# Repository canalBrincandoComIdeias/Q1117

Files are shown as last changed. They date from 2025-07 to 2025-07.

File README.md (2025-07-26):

# Q1117
**Painéis I2C para o Elevador**

Projeto do Vídeo Q1117 Série **_Tutorial Maker_** powered by **_Petrobras_**

:video_camera: Assista o vídeo [CLIQUE AQUI](https://youtu.be/gxso-JEM9QQ)

- Confira a série completa na Playlist [(Clique Aqui)](https://www.youtube.com/playlist?list=PL7CjOZ3q8fMfSiij6-3jm6nDhk7XdAp0p)

:mortar_board: Aprenda a programar ARDUINO com nossos cursos e aprenda a desenvolver sua própria lógica da programação e ter uma maior independencia, sem precisar copiar sketchs na internet.
- [Curso de Arduino para Principiantes](https://cursodearduino.net/principiantes/) 
- [Curso de Arduino 2.0](https://cursodearduino.net/)

:iphone: Todos os apps Android **Brincando com Ideias**: [CLIQUE AQUI](https://play.google.com/store/apps/developer?id=Brincando+com+Ideias&hl=pt_BR) 

 - Aplicativo montTUDO 4 canais: [CLIQUE AQUI](https://play.google.com/store/apps/details?id=appinventor.ai_thiago_vilella.montTUDO_4_Canais)
 - Aplicativo monTUDO robô: [CLIQUE AQUI](https://play.google.com/store/apps/details?id=appinventor.ai_flaviosg_2407.montTUDO_Robo)

**Conheça nossas Redes Sociais:**









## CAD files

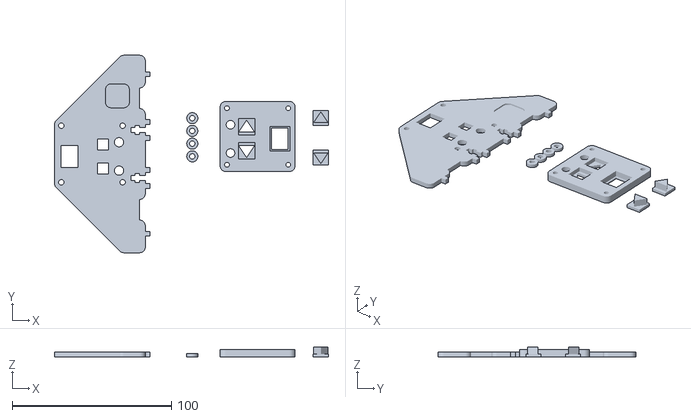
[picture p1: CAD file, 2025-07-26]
KK.128 - Painel de Andar do Elevador - Impressao.stl
172.0 x 124.0 x 6.00

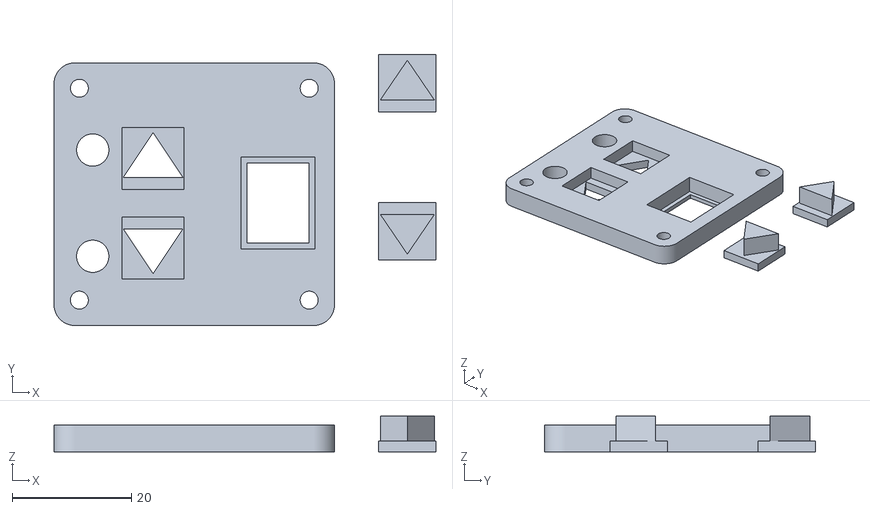
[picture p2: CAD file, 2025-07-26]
K.128 - Painel de Andar do Elevador - Impressao 3D.stl
64.0 x 45.4 x 6.00

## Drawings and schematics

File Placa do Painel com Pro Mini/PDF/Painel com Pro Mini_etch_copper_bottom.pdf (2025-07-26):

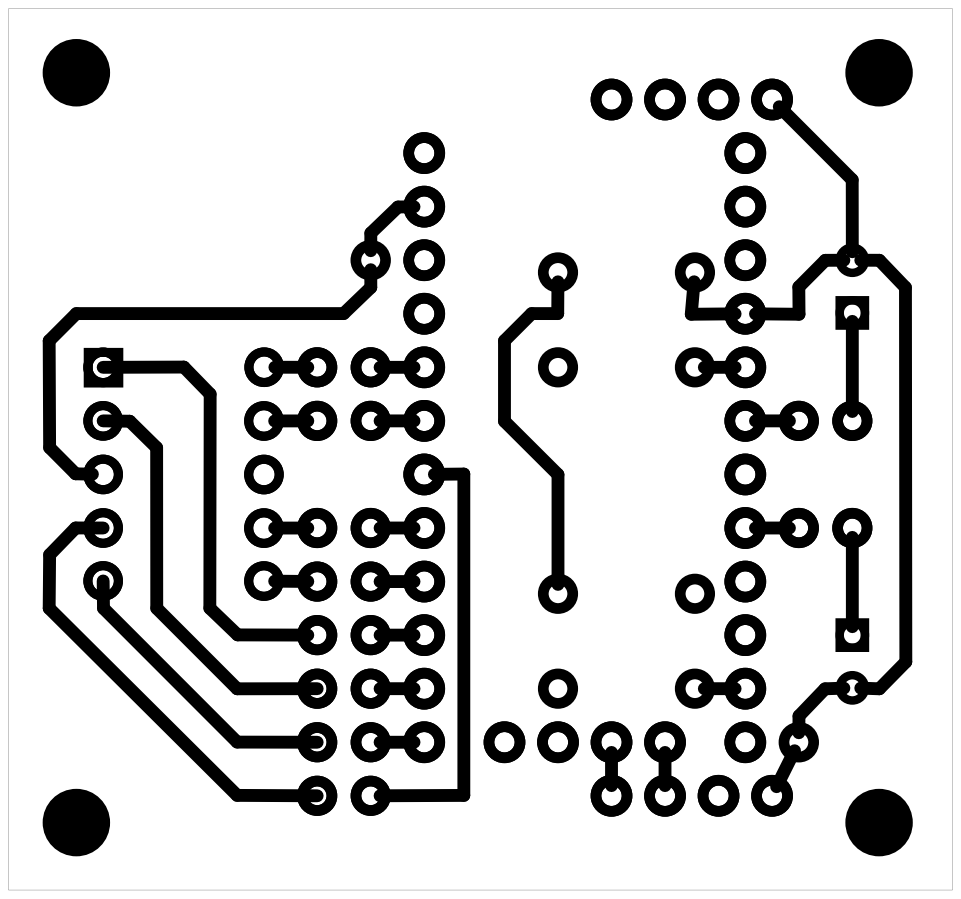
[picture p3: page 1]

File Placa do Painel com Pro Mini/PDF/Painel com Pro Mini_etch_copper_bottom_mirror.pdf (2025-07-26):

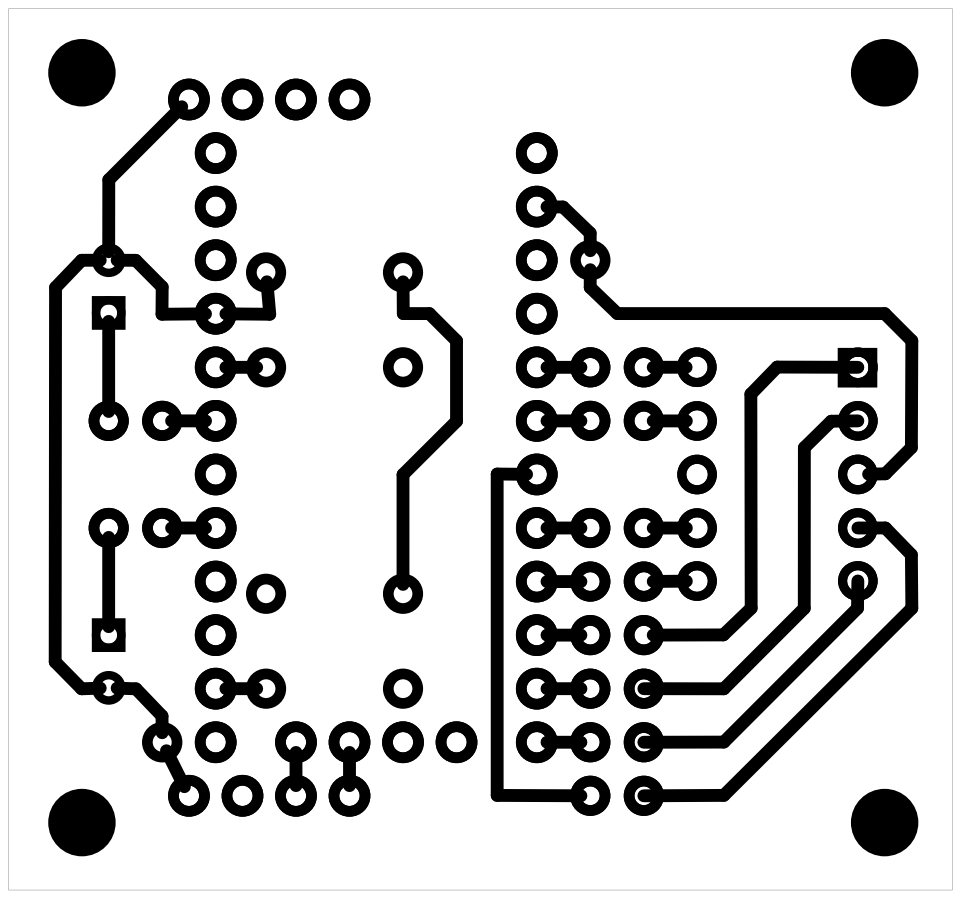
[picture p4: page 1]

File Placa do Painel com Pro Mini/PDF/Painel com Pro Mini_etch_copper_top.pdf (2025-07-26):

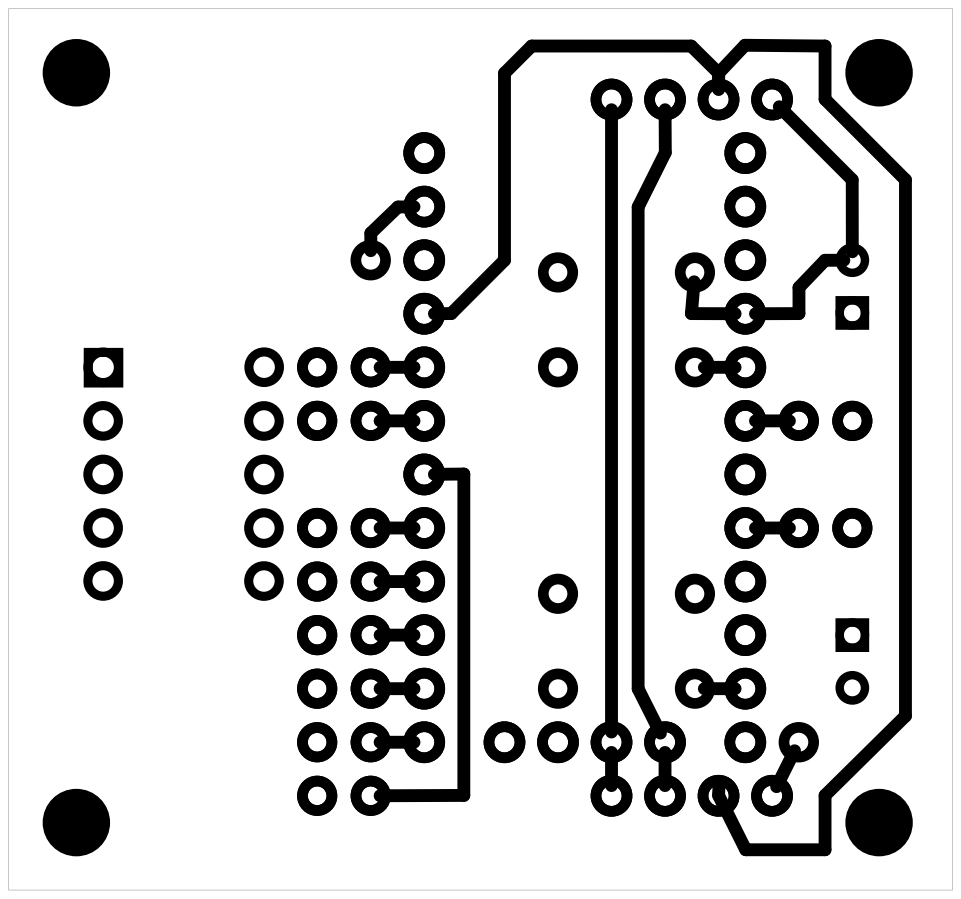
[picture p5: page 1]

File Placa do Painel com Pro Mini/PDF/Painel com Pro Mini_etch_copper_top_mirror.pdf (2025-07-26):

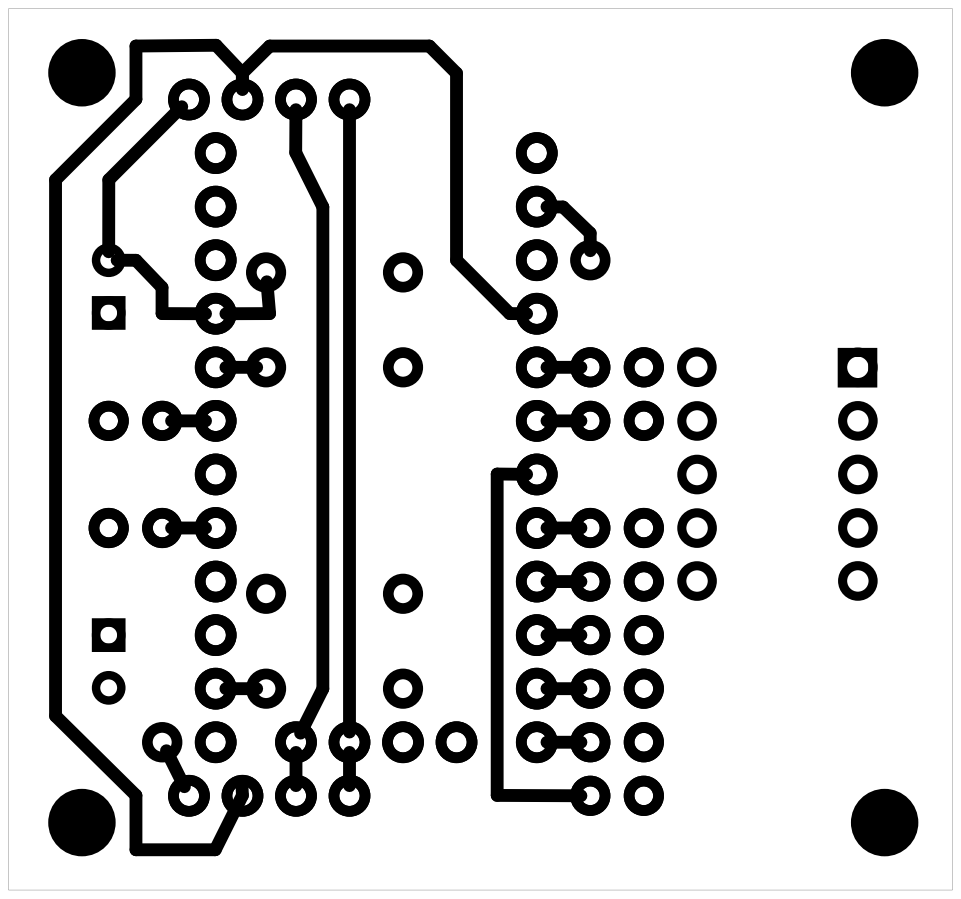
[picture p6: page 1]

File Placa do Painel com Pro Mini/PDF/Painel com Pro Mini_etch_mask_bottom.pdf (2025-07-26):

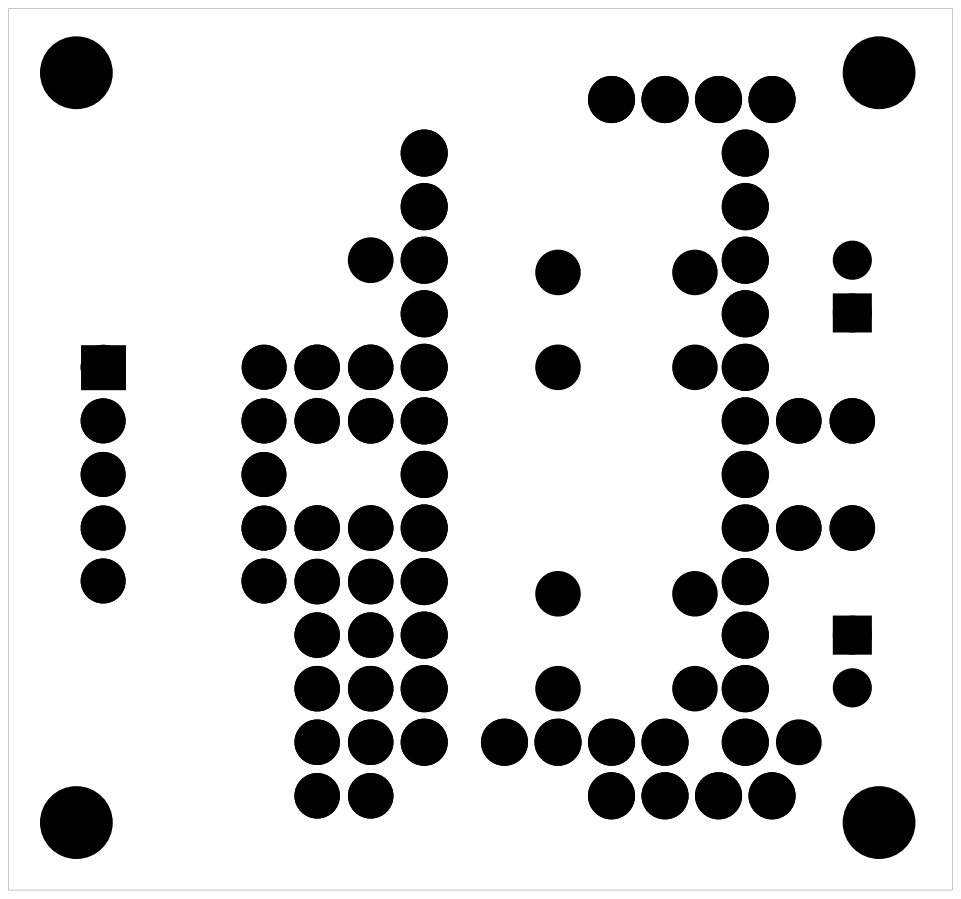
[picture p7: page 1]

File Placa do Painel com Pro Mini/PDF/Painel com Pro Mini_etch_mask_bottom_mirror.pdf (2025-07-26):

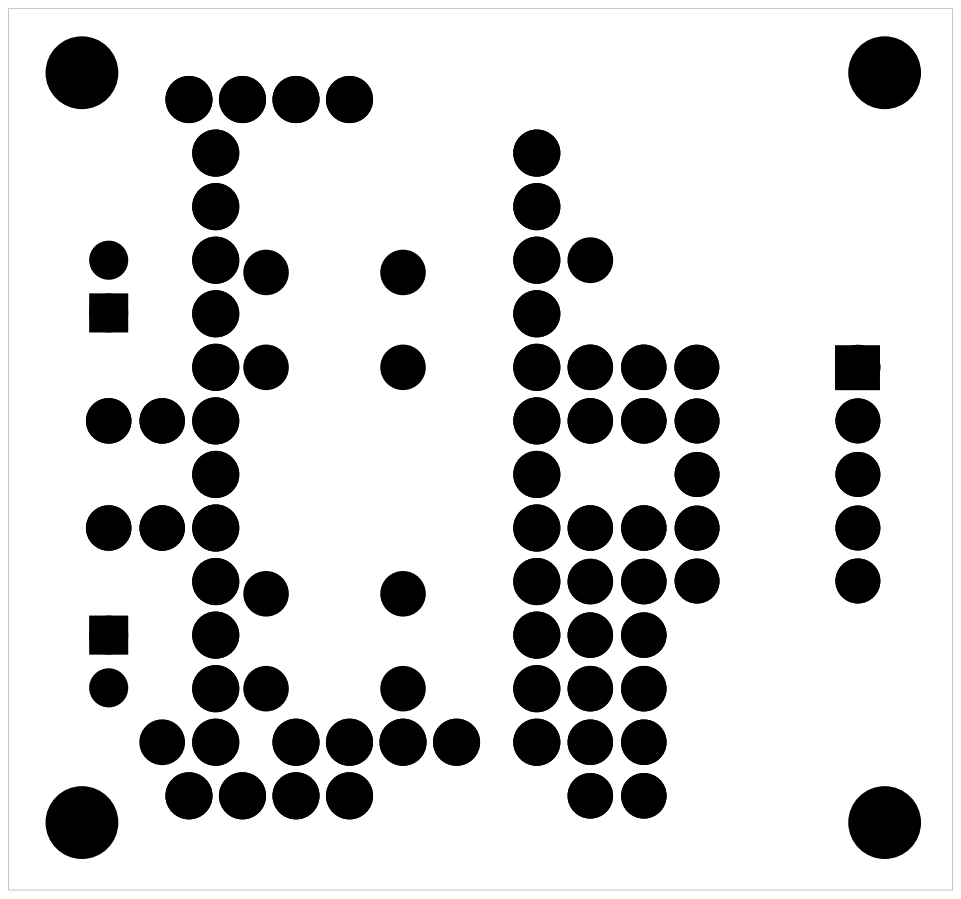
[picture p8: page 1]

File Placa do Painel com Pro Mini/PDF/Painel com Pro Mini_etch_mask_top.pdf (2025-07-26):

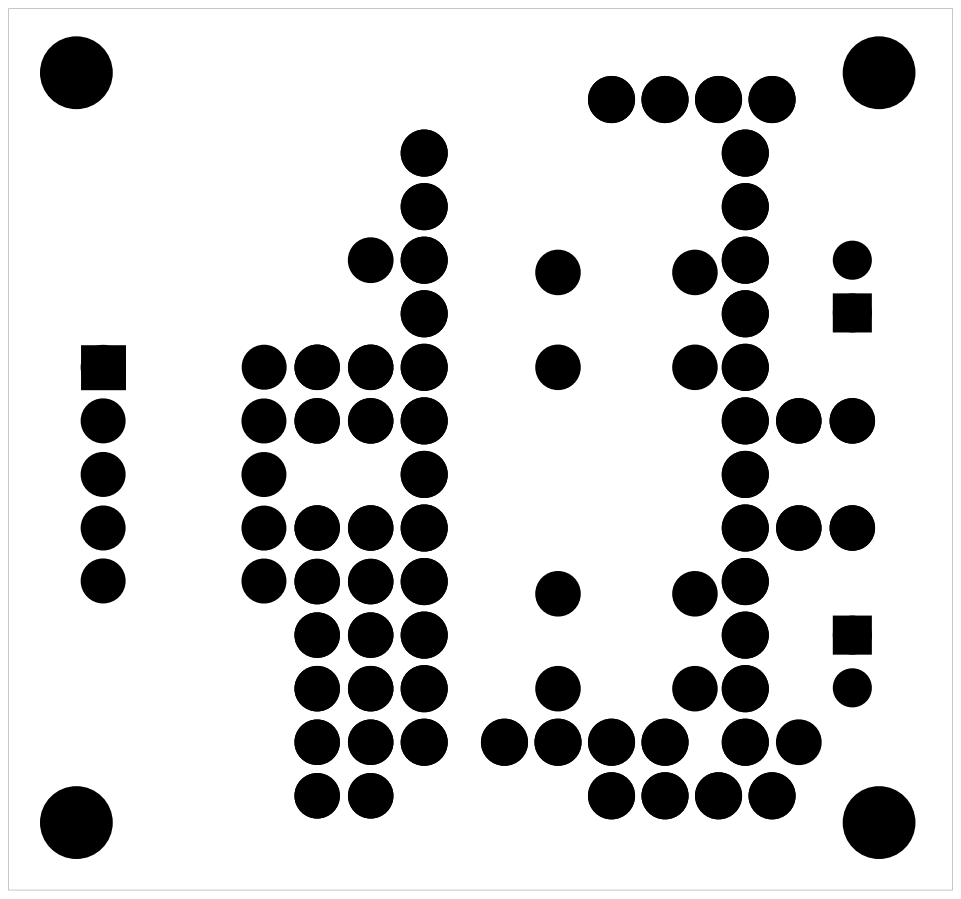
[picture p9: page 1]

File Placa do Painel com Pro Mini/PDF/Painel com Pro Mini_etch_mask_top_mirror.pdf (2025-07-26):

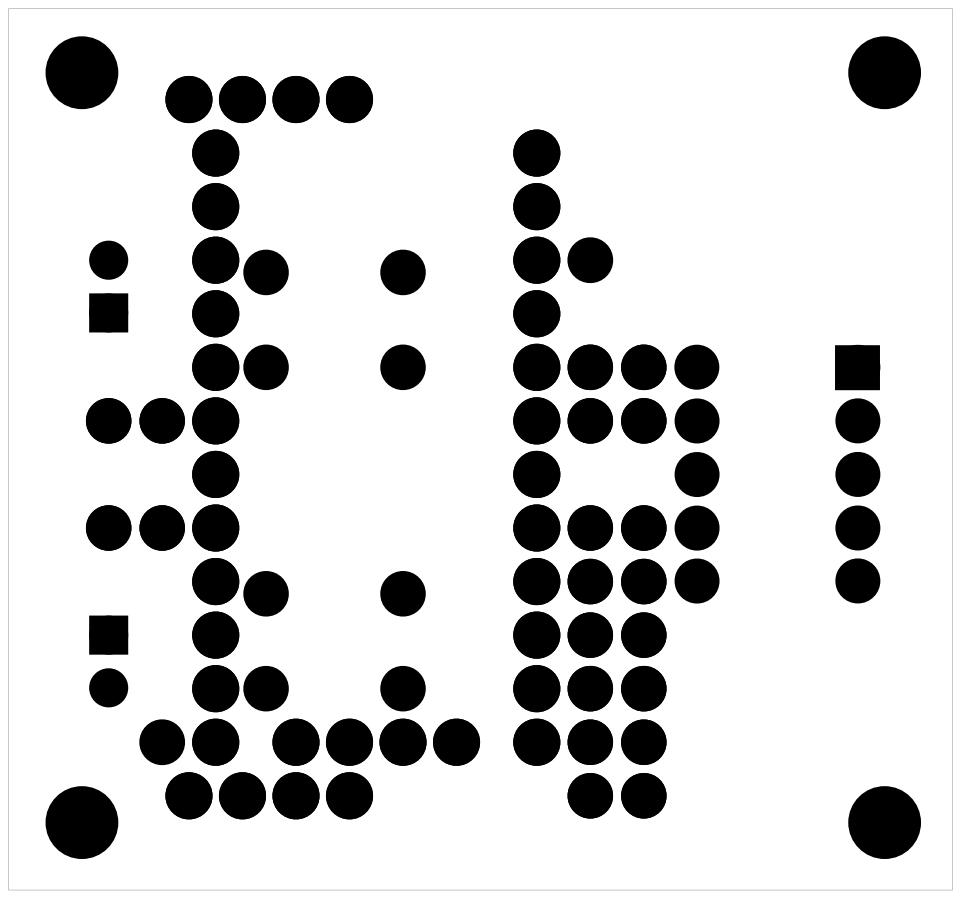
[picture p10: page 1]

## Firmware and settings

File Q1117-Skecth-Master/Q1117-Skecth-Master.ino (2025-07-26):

/****************************************************************************************
  Elevador com Motor DC
  
  Desenvolvido pela Fábrica de Programas - Brincando com Ideias (www.brincandocomideias.com)
  www.youtube.com/c/BrincandoComIdeias

  Autor Flavio Guimaraes
*****************************************************************************************/
#include <Wire.h>
#include <LiquidCrystal_I2C.h>

#define pinMotorA 9    //Motor DC
#define pinMotorB 10   //Motor DC
#define pinBotaoA 2    //Botão - Andar 1
#define pinBotaoB 3    //Botão - Andar 2
#define pinBotaoC 4    //Botão - Andar 3
#define pinBotaoD 5    //Botão - Andar 4
#define pinSensorA 8   //Sensor de Efeito Hall - Andar 1
#define pinSensorB 11  //Sensor de Efeito Hall - Andar 2
#define pinSensorC 12  //Sensor de Efeito Hall - Andar 3
#define pinSensorD 13  //Sensor de Efeito Hall - Andar 4
#define pinBuzzer 6    //Buzzer Passivo
#define pinLedA A0     //LED - Andar 1
#define pinLedB A1     //LED - Andar 2
#define pinLedC A2     //LED - Andar 3
#define pinLedD A3     //LED - Andar 4

#define velocidadeSobe 200
#define velocidadeDesce 90

LiquidCrystal_I2C lcd(0x27, 20, 4);

String ponteiro[2] = { "v", " " };
int ledAndar[4] = { pinLedA, pinLedB, pinLedC, pinLedD };
int enderecoAndar[4] = { 0x11, 0x12, 0x13, 0x14 };

bool estadoSensorA;
bool estadoSensorB;
bool estadoSensorC;
bool estadoSensorD;

bool estadoSensorAAnt;
bool estadoSensorBAnt;
bool estadoSensorCAnt;
bool estadoSensorDAnt;

int acaoElevador = 0;  //0- Parado, 1-Subindo, 2-Descendo
int acaoElevadorAnt = 0;

int andar = -1;
int andarAnt = 0;
int andarDestino = -1;
int andarDestinoAnt = -1;

void setup() {
  pinMode(pinBotaoA, INPUT_PULLUP);
  pinMode(pinBotaoB, INPUT_PULLUP);
  pinMode(pinBotaoC, INPUT_PULLUP);
  pinMode(pinBotaoD, INPUT_PULLUP);

  pinMode(pinLedA, OUTPUT);
  pinMode(pinLedB, OUTPUT);
  pinMode(pinLedC, OUTPUT);
  pinMode(pinLedD, OUTPUT);

  pinMode(pinSensorA, INPUT);
  pinMode(pinSensorB, INPUT);
  pinMode(pinSensorC, INPUT);
  pinMode(pinSensorD, INPUT);

  pinMode(pinBuzzer, OUTPUT);
  pinMode(pinMotorA, OUTPUT);
  pinMode(pinMotorB, OUTPUT);

  Wire.begin();  // Inicia o I2C como mestre

  lcd.init();
  lcd.init();
  lcd.backlight();
  lcd.setCursor(1, 0);
  lcd.print("Elevador montTUDO");

  lcd.setCursor(1, 3);              // 01234567890123456789   ->coordenadas
  lcd.print("(1)  (2)  (3)  (4)");  //  (1)  (2)  (3)  (4)

  digitalWrite(pinLedA, HIGH);
  digitalWrite(pinLedB, HIGH);
  digitalWrite(pinLedC, HIGH);
  digitalWrite(pinLedD, HIGH);

  tone(pinBuzzer, 800);
  delay(100);
  tone(pinBuzzer, 400);
  delay(100);
  tone(pinBuzzer, 800);
  delay(100);
  noTone(pinBuzzer);

  digitalWrite(pinLedA, LOW);
  digitalWrite(pinLedB, LOW);
  digitalWrite(pinLedC, LOW);
  digitalWrite(pinLedD, LOW);

  identificaAndar();

  //Atualiza o Display dos Andares e Apaga os LEDs
  for (int nL = 0; nL < 4; nL++) {
    Wire.beginTransmission(enderecoAndar[nL]);
    Wire.write(andar + '0');
    Wire.endTransmission();

    Wire.beginTransmission(enderecoAndar[nL]);
    Wire.write('S');
    Wire.endTransmission();

    Wire.beginTransmission(enderecoAndar[nL]);
    Wire.write('D');
    Wire.endTransmission();
  }
}

void loop() {

  //Controle dos botões
  if (!digitalRead(pinBotaoA)) andarDestino = 1;
  if (!digitalRead(pinBotaoB)) andarDestino = 2;
  if (!digitalRead(pinBotaoC)) andarDestino = 3;
  if (!digitalRead(pinBotaoD)) andarDestino = 4;

  //Controle das chamadas dos andares
  for (int nL = 0; nL < 4; nL++) {
    Wire.requestFrom(enderecoAndar[nL], 1);
    if (Wire.available()) {
      char command = Wire.read();
      if (command != 'N') {
        andarDestino = nL + 1;
      }
    }
  }

  //Controle das ações
  if (andar == andarDestino) acaoElevador = 0;  //Elevador precisa parar
  if (andar < andarDestino) acaoElevador = 1;   //Elevador precisa subir
  if (andar > andarDestino) acaoElevador = 2;   //Elevador precisa descer

  //Controle dos andares
  estadoSensorA = !digitalRead(pinSensorA);
  estadoSensorB = !digitalRead(pinSensorB);
  estadoSensorC = !digitalRead(pinSensorC);
  estadoSensorD = !digitalRead(pinSensorD);

  if (estadoSensorA && !estadoSensorAAnt) andar = 1;
  if (estadoSensorB && !estadoSensorBAnt) andar = 2;
  if (estadoSensorC && !estadoSensorCAnt) andar = 3;
  if (estadoSensorD && !estadoSensorDAnt) andar = 4;

  //Executa a ação de acordo com o estado do elevador e os comandos recebidos pelos botões
  if (acaoElevador == 0) {
    if (acaoElevadorAnt == 1) {  //Estava subindo. Entao freia para baixo.
      analogWrite(pinMotorA, 255);
      analogWrite(pinMotorB, 255);
      tone(pinBuzzer, 800);
      delay(40);
      noTone(pinBuzzer);
    }
    if (acaoElevadorAnt == 2) {  //Estava descendo. Entao freia para cima.
      analogWrite(pinMotorA, 0);
      analogWrite(pinMotorB, velocidadeSobe);
      tone(pinBuzzer, 800);
      delay(40);
      noTone(pinBuzzer);
    }
    analogWrite(pinMotorA, 255);
    analogWrite(pinMotorB, 255);

    digitalWrite(pinLedA, LOW);
    digitalWrite(pinLedB, LOW);
    digitalWrite(pinLedC, LOW);
    digitalWrite(pinLedD, LOW);

    Wire.beginTransmission(enderecoAndar[andarDestino - 1]);
    Wire.write('S');
    Wire.endTransmission();

    Wire.beginTransmission(enderecoAndar[andarDestino - 1]);
    Wire.write('D');
    Wire.endTransmission();
  } else {
    digitalWrite(ledAndar[andarDestino - 1], HIGH);
  }

  if (acaoElevador == 1) {  //Subir o elevador
    analogWrite(pinMotorA, 0);
    analogWrite(pinMotorB, velocidadeSobe);
  }

  if (acaoElevador == 2) {  //Descer o elevador
    analogWrite(pinMotorA, velocidadeDesce);
    analogWrite(pinMotorB, 0);
  }

  //Atualiza o ponteiro dos andares no display
  lcd.setCursor(2, 2);
  lcd.print(ponteiro[digitalRead(pinSensorA)]);
  lcd.setCursor(7, 2);
  lcd.print(ponteiro[digitalRead(pinSensorB)]);
  lcd.setCursor(12, 2);
  lcd.print(ponteiro[digitalRead(pinSensorC)]);
  lcd.setCursor(17, 2);
  lcd.print(ponteiro[digitalRead(pinSensorD)]);

  //Atualiza o display dos andares
  for (int nL = 0; nL < 4; nL++) {
    Wire.beginTransmission(enderecoAndar[nL]);
    Wire.write(andar + '0');
    Wire.endTransmission();
  }

  estadoSensorAAnt = estadoSensorA;
  estadoSensorBAnt = estadoSensorB;
  estadoSensorCAnt = estadoSensorC;
  estadoSensorDAnt = estadoSensorD;

  acaoElevadorAnt = acaoElevador;
  andarAnt = andar;
  andarDestinoAnt = andarDestino;
}

void identificaAndar() {

  estadoSensorA = !digitalRead(pinSensorA);
  estadoSensorB = !digitalRead(pinSensorB);
  estadoSensorC = !digitalRead(pinSensorC);
  estadoSensorD = !digitalRead(pinSensorD);

  andar = -1;
  if (estadoSensorA) andar = 1;
  if (estadoSensorB) andar = 2;
  if (estadoSensorC) andar = 3;
  if (estadoSensorD) andar = 4;

  //Caso nenhum sensor detectado, desce o elevador até que um seja encontrado.
  if (andar == -1) {
    analogWrite(pinMotorA, velocidadeDesce);
    analogWrite(pinMotorB, 0);

    do {

      estadoSensorA = !digitalRead(pinSensorA);
      estadoSensorB = !digitalRead(pinSensorB);
      estadoSensorC = !digitalRead(pinSensorC);
      estadoSensorD = !digitalRead(pinSensorD);

      if (estadoSensorA) andar = 1;
      if (estadoSensorB) andar = 2;
      if (estadoSensorC) andar = 3;
      if (estadoSensorD) andar = 4;

      if (andar != -1) {
        analogWrite(pinMotorA, 0);
        analogWrite(pinMotorB, velocidadeSobe);
        tone(pinBuzzer, 800);
        delay(40);
        noTone(pinBuzzer);
        analogWrite(pinMotorA, 255);
        analogWrite(pinMotorB, 255);

        break;
      }
    } while (andar == -1);
  }

  andarDestino = andar;
}

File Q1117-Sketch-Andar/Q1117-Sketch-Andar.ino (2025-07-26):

// Código para os Arduinos Pro Mini (Slaves)
#include <Wire.h>

#define pinLEDVd 3
#define pinLEDVm 5

#define pinSegA A3
#define pinSegB A2
#define pinSegC A0
#define pinSegD 10
#define pinSegE A1
#define pinSegF 11
#define pinSegG 12
#define pinSegDP 13

#define pinBotaoSobe 2
#define pinBotaoDesce 8

// Defina o endereço I2C deste Pro Mini
#define I2C_ADDRESS 0x11  // Andar 1: endereço 0x11, Andar 2: endereço 0x12

int portas[8] = { pinSegA, pinSegB, pinSegC, pinSegD, pinSegE, pinSegF, pinSegG, pinSegDP };

//a b c d e f g dp
bool digitos[10][8] = {
  { 1, 1, 1, 1, 1, 1, 0, 0 },  //0
  { 0, 1, 1, 0, 0, 0, 0, 0 },  //1
  { 1, 1, 0, 1, 1, 0, 1, 0 },  //2
  { 1, 1, 1, 1, 0, 0, 1, 0 },  //3
  { 0, 1, 1, 0, 0, 1, 1, 0 },  //4
  { 1, 0, 1, 1, 0, 1, 1, 0 },  //5
  { 1, 0, 1, 1, 1, 1, 1, 0 },  //6
  { 1, 1, 1, 0, 0, 0, 0, 0 },  //7
  { 1, 1, 1, 1, 1, 1, 1, 0 },  //8
  { 1, 1, 1, 1, 0, 1, 1, 0 }   //9
};

unsigned long delayInc;
int andar = 0;
bool estadoChamadaSobe = false;
bool estadoChamadaDesce = false;

void setup() {
  pinMode(pinLEDVd, OUTPUT);
  pinMode(pinLEDVm, OUTPUT);
  pinMode(pinSegA, OUTPUT);
  pinMode(pinSegB, OUTPUT);
  pinMode(pinSegC, OUTPUT);
  pinMode(pinSegD, OUTPUT);
  pinMode(pinSegE, OUTPUT);
  pinMode(pinSegF, OUTPUT);
  pinMode(pinSegG, OUTPUT);
  pinMode(pinSegDP, OUTPUT);

  pinMode(pinBotaoSobe, INPUT_PULLUP);
  pinMode(pinBotaoDesce, INPUT_PULLUP);

  Wire.begin(I2C_ADDRESS);  // Inicializa o I2C com o endereço específico
  Wire.onReceive(recebeDados);
  Wire.onRequest(enviarDados);
}

void loop() {

  //Botão "sobe" acionado
  if (!digitalRead(pinBotaoSobe)) {
    estadoChamadaSobe = true;
  }

  //Botão "desce" acionado
  if (!digitalRead(pinBotaoDesce)) {
    estadoChamadaDesce = true;
  }

  digitalWrite(pinLEDVd, estadoChamadaSobe);
  digitalWrite(pinLEDVm, estadoChamadaDesce);
}

void recebeDados(int num_bytes) {
  char command = Wire.read();
  if ((command >= '0') && (command <= '9')) {
    andar = command - '0';
    for (int nL = 0; nL < 8; nL++) {
      digitalWrite(portas[nL], digitos[andar][nL]);
    }
  }

  if (command == 'S') {  //Considerar chamada para cima como atendida
    estadoChamadaSobe = false;
  }

  if (command == 'D') {  //Considerar chamada para baixo como atendida
    estadoChamadaDesce = false;
  }
}

void enviarDados() {
  if (estadoChamadaSobe) {
    if (estadoChamadaDesce) {
       Wire.write('A');  //Ambos botões apertados
    } else {
       Wire.write('S');  //Botão sobe apertado
    }
  } else {
    if (estadoChamadaDesce) {
       Wire.write('D');  //Botão desce apertado
    } else {
       Wire.write('N');  //Nenhum botão apertado
    }
  }
}
